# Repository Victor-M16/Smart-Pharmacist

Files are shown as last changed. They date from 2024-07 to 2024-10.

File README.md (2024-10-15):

# Smart Pharmacist

This project repository holds architecture and website source code for the Smart Pharmacist final year engineering project being implemented at [Malawi University Of Business And Applied Sciences](https://www.mubas.ac.mw/) by Victor Mjimapemba, Khumbolawo Mussa and Grace Chiwaya.

The project consists of a hardware and software element. The hardware element is an electronics project that is a rudimentary prototype of a carousel vending machine meant to dispense prescription medication. Further documentation for these componenents can be found in the `firmware` and `concepts` folders.

The software component is a built from the ground up hospital management system meant to work in tandem with the prototype. The main system is a django project named `smartpharmacist`

## Use Case Workflow
1. The patient completes a consultation with the doctor, who enters the prescription details into the web system, such as the patient's name, sickness and prescribed medication and instructions to take the medications.
2. The system automatically generates a unique 4-digit "prescription.code" which it assigns to the prescription the doctor just submitted.
3. The system sends an SMS message to the patient, containing the prescription.code, the names of the prescribed medications and the associated instructions. If the patient has no phone or their phone is off, the code is also displayed on the doctor's screen so the patient can copy it down on a paper or their physical health passport. 
4. The patient goes to the vennding machine prototype,which has already been boooted, has authenticated itself with the backend server using `jwt` and gone into `ready-state`. The patient then inputs the received "prescription.code" on the numeric keypad, using visual feedback from the 16x2 LCD module.
5. The machine goes into `code-validation-state` where it sends the received code to the backend server for processing as a POST request for security.
6. The backend server checks the code against its prescriptions database and if the code exists and corresponds to a prescription that has not been dispensed yet, then it queries the database for the medications assigned to this prescription and the vending slots where these pre-packaged medications were stored. The server responds to to the vending machine after this processing with either an error message if the code was invalid or a list of vending slots in optimised order for the vending machine to rotate to if the code was valid.
7. If the vending machine received a list of vending slots, then it goes into `dispensing-state` where it rotates in order of the received slots, allowing the patient to collect all their assigned medications.
8. The vending machine updates the prescription in the database so that itself and other vending machines know that that prescription code is no longer valid and has been dispensed.
9. The vending machine goes back into `ready-state` to be ready to service the next patient and code.

## Technologies 

1. [Django](https://docs.djangoproject.com/en/5.1/)
2. [Django-Rest-FrameWork](https://www.django-rest-framework.org/)
3. [HTML/CSS](https://developer.mozilla.org/en-US/docs/Learn/HTML/Introduction_to_HTML/Getting_started)
4. [Tailwind CSS](https://tailwindcss.com/)
5. [ArduinoIDE](https://www.arduino.cc/en/Guide)
6. [Twilio](https://www.twilio.com/en-us)
7. [Postgres](https://www.postgresql.org/)

## Hardware 

1. 16x2 LCD module. Ours uses (0x27) addressing. You need to check this.
2. ESP32
3. Arduino Uno
4. 4X4 Matrix Keypad
5. NEMA 17 Motors (17HS4023)
6. L298N Motor Drivers
7. Buzzer
8. Switch

## Setting Up The Project

1. Fork and clone this repository

2. Setup your Django development environment. More instructions [here](https://www.djangoproject.com/start/)

3. Make sure to also have node.js installed. Instructions [here](https://nodejs.org/)

4. Create a python virtual environment in the `smartpharmacist` directory

5. Install Django dependencies for the project using the `requirements.txt`

```shell
pip install requirements.txt
```
6. Install django-tailwind dependencies by navigating to `theme\static_src\` in your terminal and typing 

```shell
npm install
```
7. Create a `local_settings.py` file in the `smartpharmacist` directory and include the following Python code

```python
from .base_settings import *
```
Here you can specify any extra configuration specification to your environment, such as database connection.

8. Start the Tailwind Development server by running the following command in your terminal

```shell
python manage.py tailwind start
```

9. Start the Django development server by running the following command in your terminal:

```shell
python manage.py runserver
```

## Contributing To The Project

Feel free to contact the developers with any contributions you would like to make

- [Victor Mjimapemba](https://github.com/Victor-M16/)

- [Khumbolawo Mussa](https://github.com/Khumbolawo/)

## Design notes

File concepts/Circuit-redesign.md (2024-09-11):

Here’s a breakdown of the wiring and code examples for controlling a **stepper motor**, **16x2 LCD via I2C**, and a **4x4 keypad** with the ESP32.

### Wiring Diagrams:

#### 1. **Stepper Motor with L298N Motor Driver**:
- **IN1 (L298N)** → **GPIO 14 (ESP32)**
- **IN2 (L298N)** → **GPIO 27 (ESP32)**
- **IN3 (L298N)** → **GPIO 26 (ESP32)**
- **IN4 (L298N)** → **GPIO 25 (ESP32)**
- **GND (L298N)** → **GND (ESP32)**
- **12V power supply** for the motor should be connected to the L298N’s **power input**.

#### 2. **16x2 LCD with I2C Module**:
- **SDA (LCD)** → **GPIO 21 (ESP32)**
- **SCL (LCD)** → **GPIO 22 (ESP32)**
- **VCC** → **3.3V or 5V (ESP32)** (depending on your LCD module voltage requirements)
- **GND (LCD)** → **GND (ESP32)**

#### 3. **4x4 Keypad**:
- **Row 1 (Keypad)** → **GPIO 33 (ESP32)**
- **Row 2 (Keypad)** → **GPIO 32 (ESP32)**
- **Row 3 (Keypad)** → **GPIO 18 (ESP32)**
- **Row 4 (Keypad)** → **GPIO 19 (ESP32)**
- **Column 1 (Keypad)** → **GPIO 4 (ESP32)**
- **Column 2 (Keypad)** → **GPIO 5 (ESP32)**
- **Column 3 (Keypad)** → **GPIO 16 (ESP32)**
- **Column 4 (Keypad)** → **GPIO 17 (ESP32)**

---

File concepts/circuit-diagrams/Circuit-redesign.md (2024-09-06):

Here’s a breakdown of the wiring and code examples for controlling a **stepper motor**, **16x2 LCD via I2C**, and a **4x4 keypad** with the ESP32.

### Wiring Diagrams:

#### 1. **Stepper Motor with L298N Motor Driver**:
- **IN1 (L298N)** → **GPIO 13 (ESP32)**
- **IN2 (L298N)** → **GPIO 12 (ESP32)**
- **IN3 (L298N)** → **GPIO 14 (ESP32)**
- **IN4 (L298N)** → **GPIO 27 (ESP32)**
- **GND (L298N)** → **GND (ESP32)**
- **12V power supply** for the motor should be connected to the L298N’s **power input**.

#### 2. **16x2 LCD with I2C Module**:
- **SDA (LCD)** → **GPIO 21 (ESP32)**
- **SCL (LCD)** → **GPIO 22 (ESP32)**
- **VCC** → **3.3V or 5V (ESP32)** (depending on your LCD module voltage requirements)
- **GND (LCD)** → **GND (ESP32)**

#### 3. **4x4 Keypad**:
- **Row 1 (Keypad)** → **GPIO 32 (ESP32)**
- **Row 2 (Keypad)** → **GPIO 33 (ESP32)**
- **Row 3 (Keypad)** → **GPIO 25 (ESP32)**
- **Row 4 (Keypad)** → **GPIO 26 (ESP32)**
- **Column 1 (Keypad)** → **GPIO 34 (ESP32)**
- **Column 2 (Keypad)** → **GPIO 35 (ESP32)**
- **Column 3 (Keypad)** → **GPIO 36 (ESP32)**
- **Column 4 (Keypad)** → **GPIO 39 (ESP32)**

---

### Code Examples:

#### 1. **Stepper Motor Control** (via L298N):
Here’s a basic code for controlling the stepper motor using the L298N motor driver with the ESP32.

```python
import RPi.GPIO as GPIO
import time

# Pin Definitions for L298N
IN1 = 13
IN2 = 12
IN3 = 14
IN4 = 27

# Setup
GPIO.setmode(GPIO.BCM)
GPIO.setup(IN1, GPIO.OUT)
GPIO.setup(IN2, GPIO.OUT)
GPIO.setup(IN3, GPIO.OUT)
GPIO.setup(IN4, GPIO.OUT)

# Step sequence for the motor
step_sequence = [
    [GPIO.HIGH, GPIO.LOW, GPIO.HIGH, GPIO.LOW],
    [GPIO.LOW, GPIO.HIGH, GPIO.HIGH, GPIO.LOW],
    [GPIO.LOW, GPIO.HIGH, GPIO.LOW, GPIO.HIGH],
    [GPIO.HIGH, GPIO.LOW, GPIO.LOW, GPIO.HIGH]
]

def step_motor(delay, steps):
    for i in range(steps):
        for step in step_sequence:
            GPIO.output(IN1, step[0])
            GPIO.output(IN2, step[1])
            GPIO.output(IN3, step[2])
            GPIO.output(IN4, step[3])
            time.sleep(delay)

try:
    # Example: Run motor for 200 steps
    step_motor(0.01, 200)
except KeyboardInterrupt:
    pass
finally:
    GPIO.cleanup()
```

#### 2. **I2C LCD Control** (Using `LiquidCrystal_I2C` library):
You'll need the `LiquidCrystal_I2C` library to control the LCD. Install the library first:

```bash
pip install RPLCD
```

Code to display a message on the LCD:

```python
from RPLCD.i2c import CharLCD

# Initialize LCD (I2C address might differ)
lcd = CharLCD('PCF8574', 0x27)

# Clear display and show "Ready"
lcd.clear()
lcd.write_string('Ready')

# Move cursor and write on second row
lcd.cursor_pos = (1, 0)
lcd.write_string('Enter Code')
```

#### 3. **4x4 Keypad Input**:
You'll need the **Keypad library**. Install the `micropython-keypad` package.

```bash
pip install micropython-keypad
```

Here’s how to read input from the 4x4 keypad:

```python
from machine import Pin
from keypad import Keypad

# Define Keypad row and column pins
rows = [Pin(32, Pin.IN), Pin(33, Pin.IN), Pin(25, Pin.IN), Pin(26, Pin.IN)]
cols = [Pin(34, Pin.IN), Pin(35, Pin.IN), Pin(36, Pin.IN), Pin(39, Pin.IN)]

# Keypad matrix (4x4)
keys = [
    ['1', '2', '3', 'A'],
    ['4', '5', '6', 'B'],
    ['7', '8', '9', 'C'],
    ['*', '0', '#', 'D']
]

keypad = Keypad(keys, rows, cols)

def get_key():
    key = keypad.getKey()
    if key:
        print(f"Key pressed: {key}")
        return key

# Loop to capture keypad input
while True:
    key = get_key()
    if key:
        lcd.clear()
        lcd.write_string(f"Key Pressed: {key}")
```

### Integration:
- Once you have each of the components working individually, you can combine them into a single program where:
  - The **keypad** allows the user to input a code.
  - The **LCD** displays the input or other messages.
  - The **motor** runs based on keypad input or another trigger.

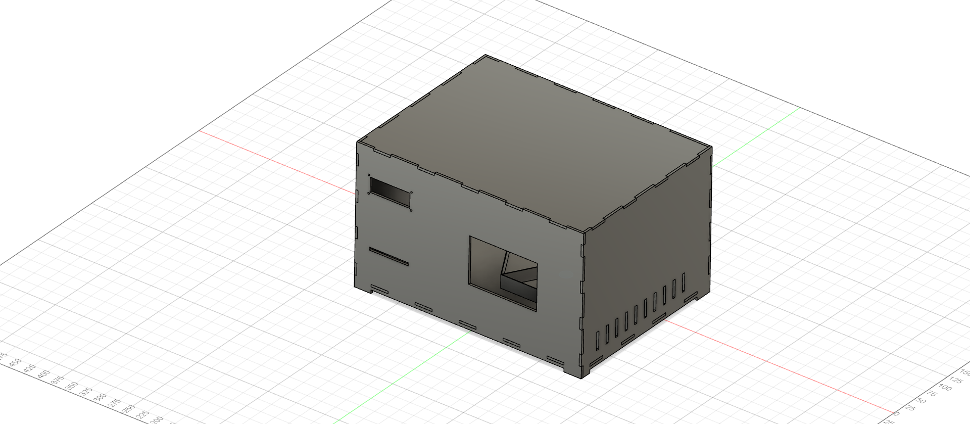
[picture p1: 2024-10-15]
concepts/3d-designs/SmartPharmacist.png

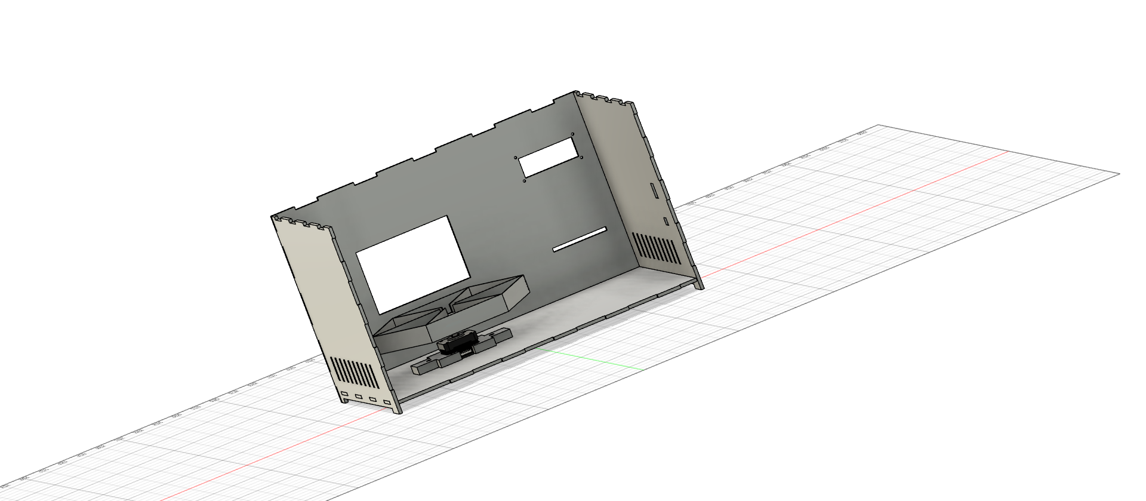
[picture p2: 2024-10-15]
concepts/3d-designs/Open.png

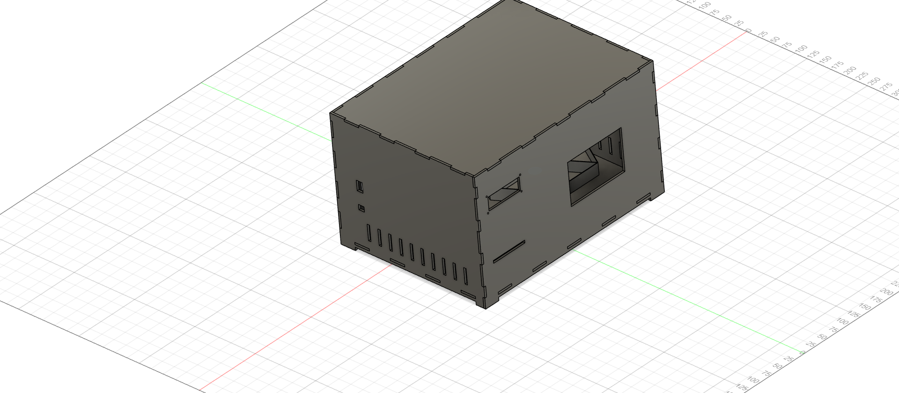
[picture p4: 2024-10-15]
concepts/3d-designs/Smart pharm.png

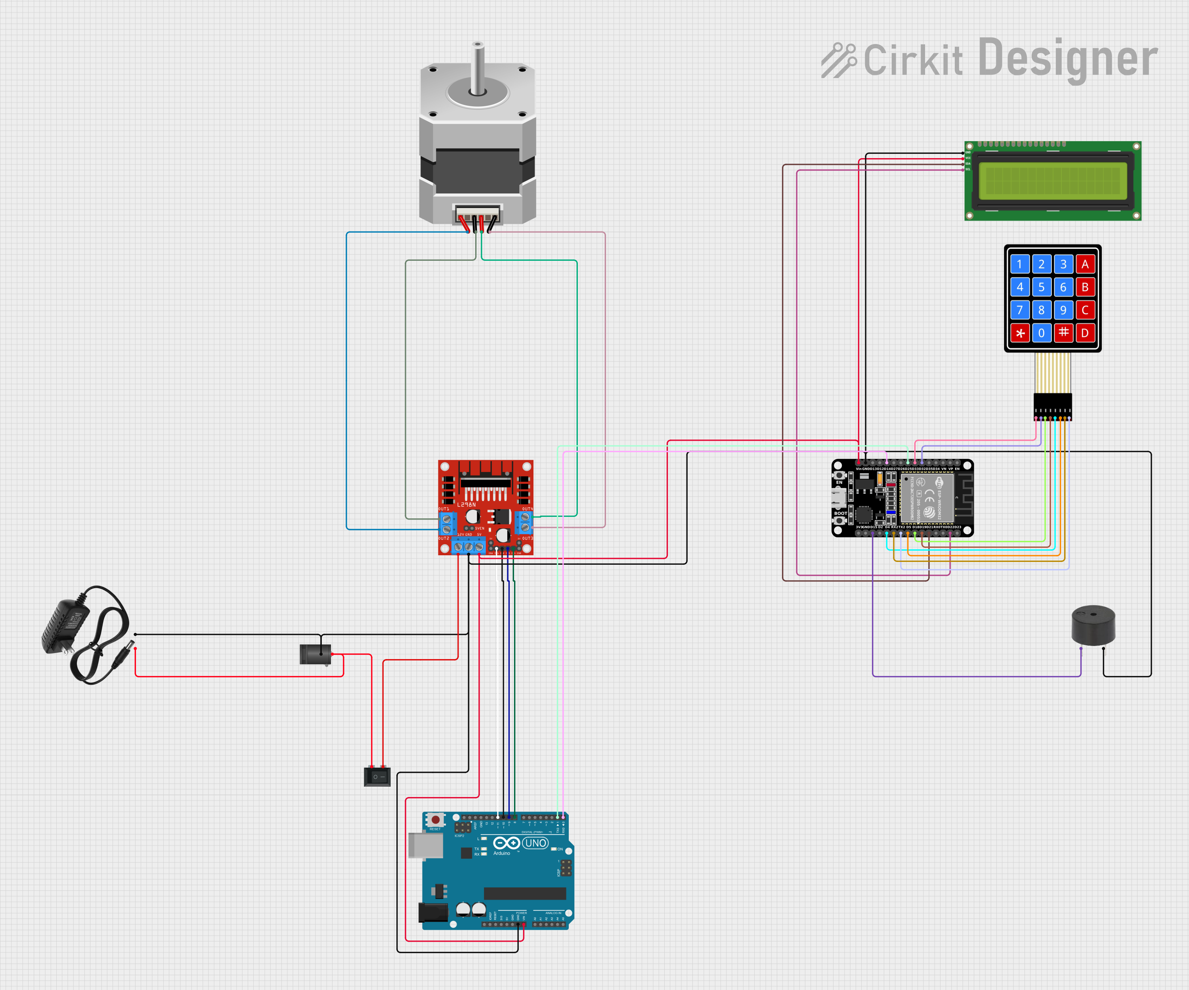
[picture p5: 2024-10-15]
concepts/circuit-diagrams/circuit_image.png

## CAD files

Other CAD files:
concepts/3d-designs/Casing v2.f3z

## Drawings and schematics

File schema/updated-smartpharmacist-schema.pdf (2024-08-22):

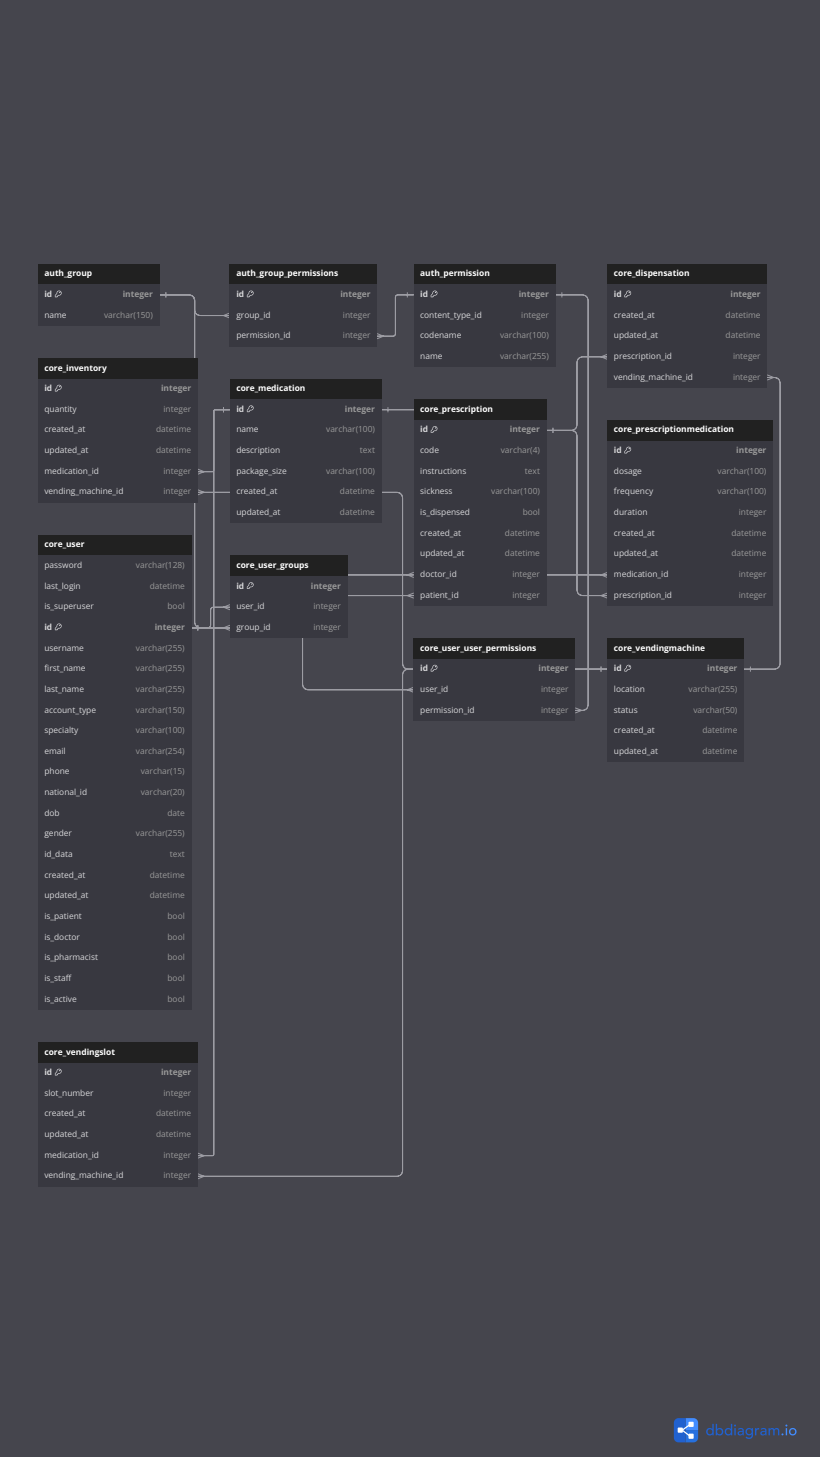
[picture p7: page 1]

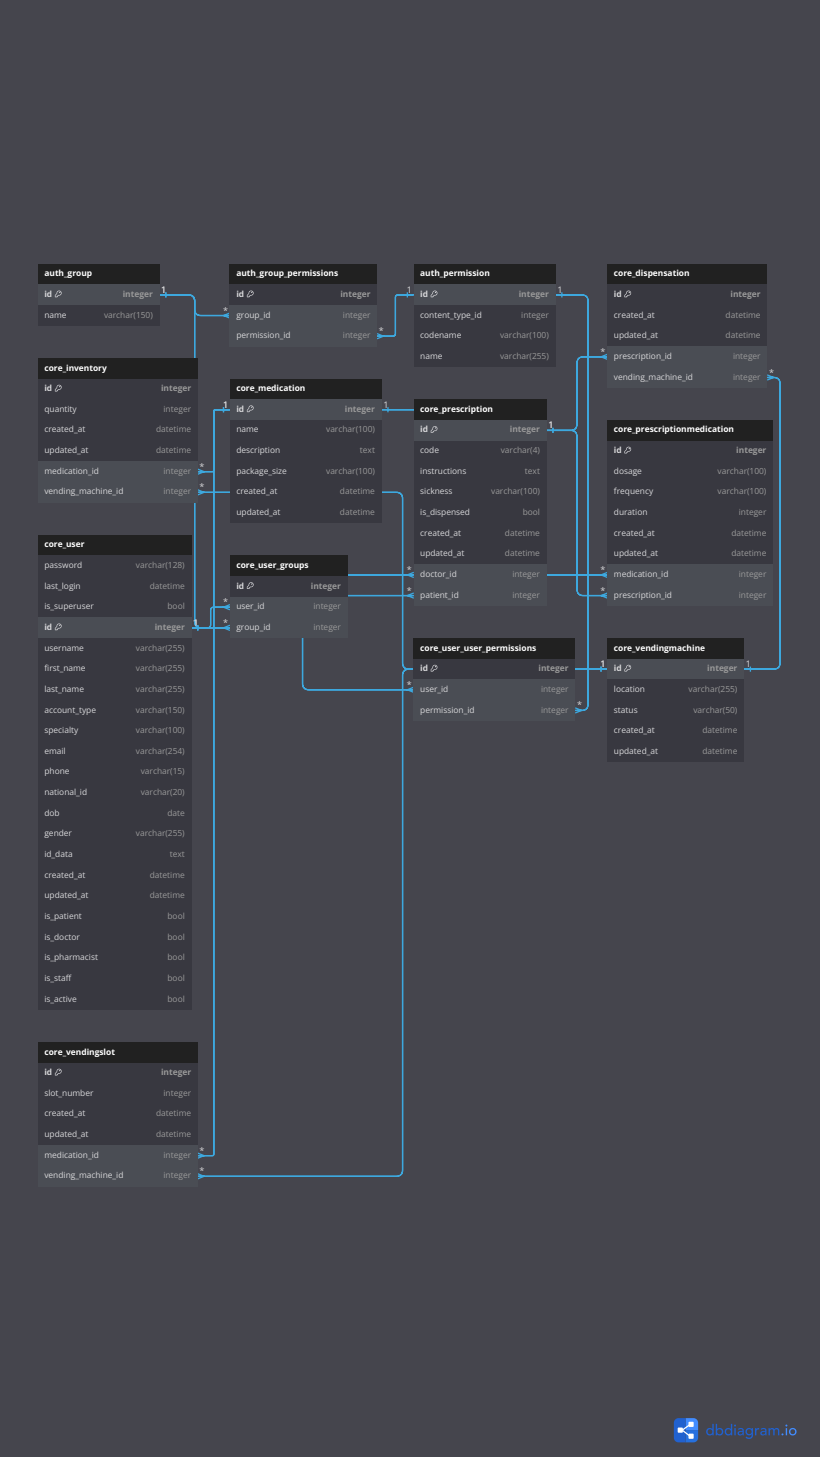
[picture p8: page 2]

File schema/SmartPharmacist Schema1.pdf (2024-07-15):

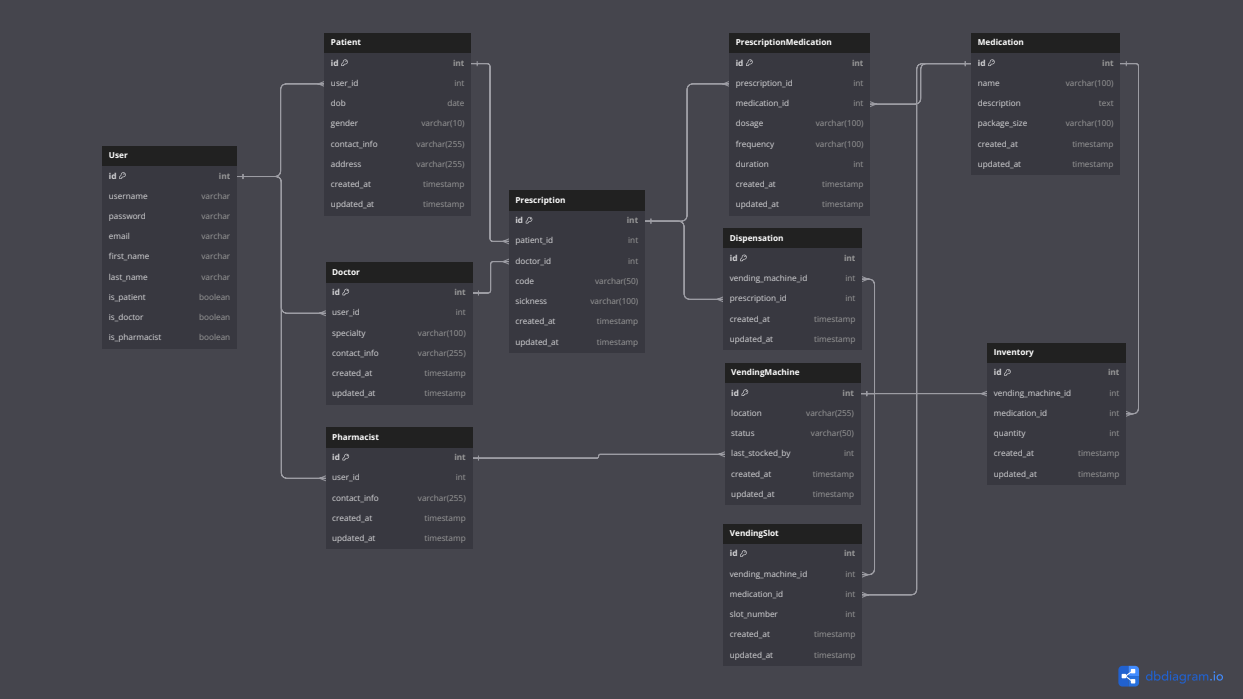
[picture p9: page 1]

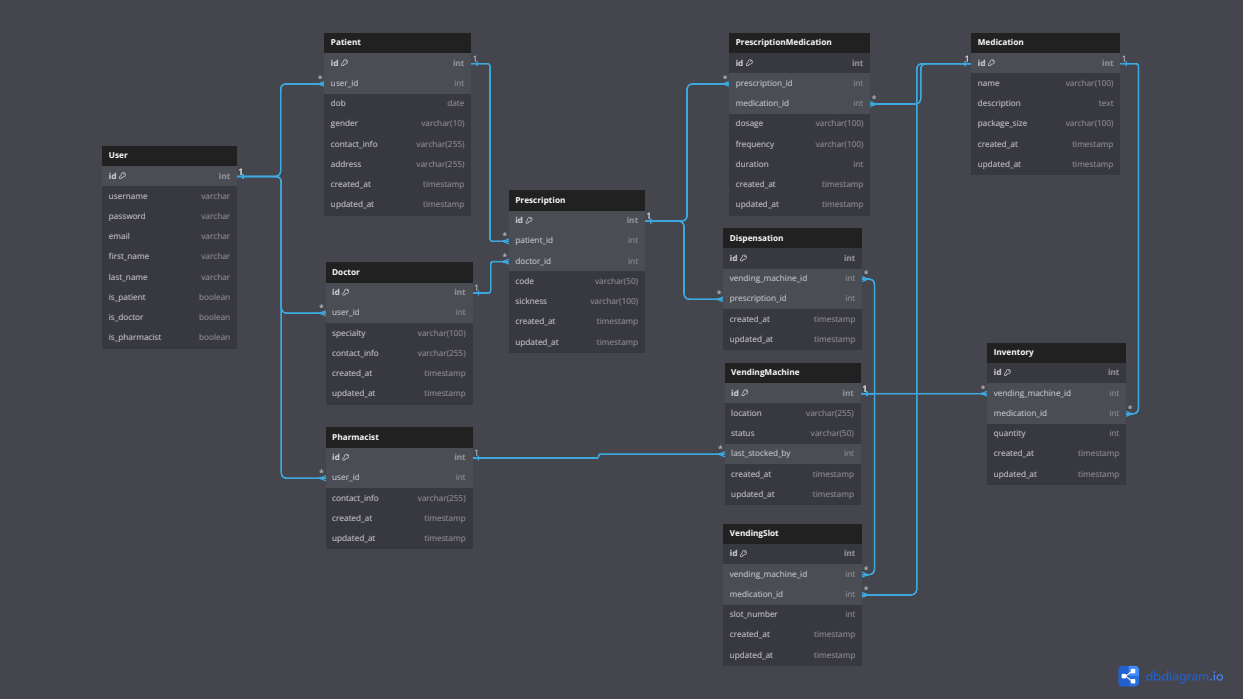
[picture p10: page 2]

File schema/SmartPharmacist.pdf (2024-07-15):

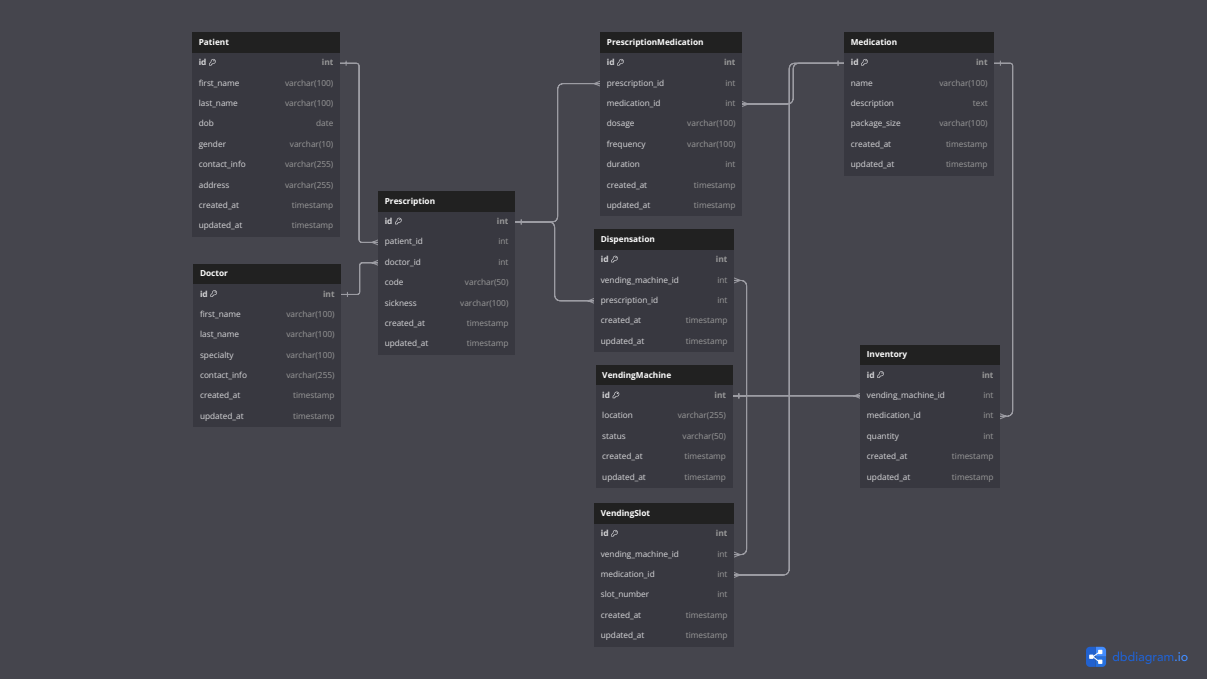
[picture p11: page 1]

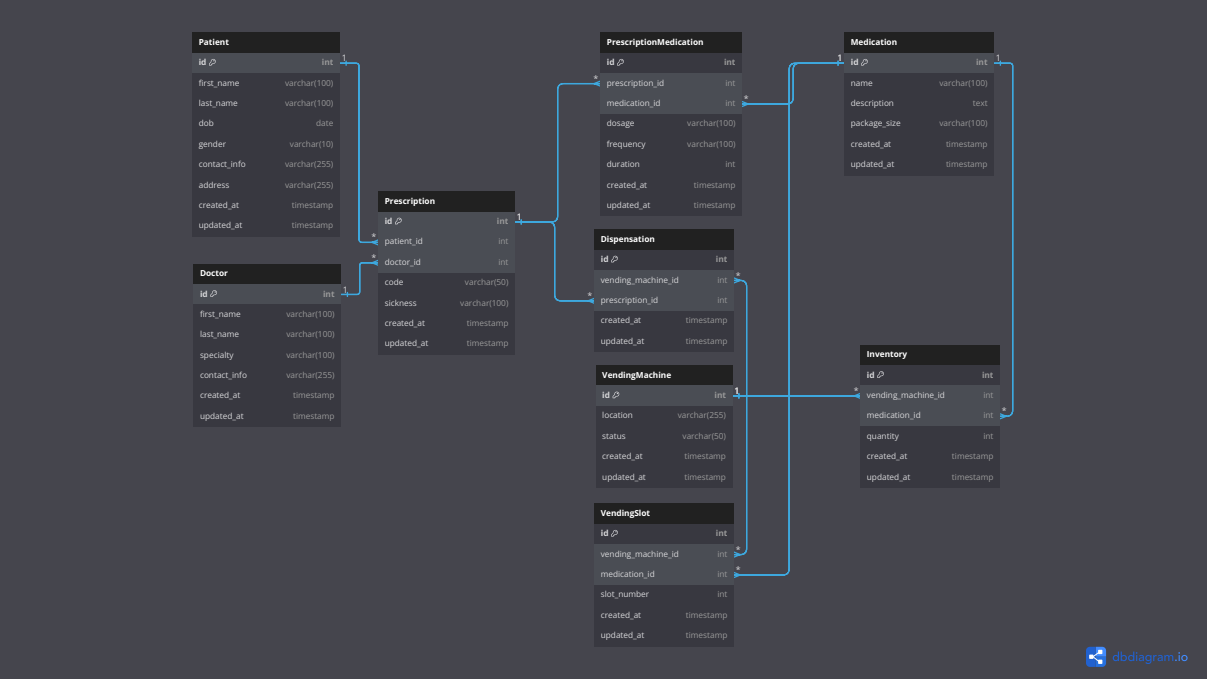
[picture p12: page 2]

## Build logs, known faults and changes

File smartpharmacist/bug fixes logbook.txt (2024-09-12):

The favicon was causing an internal server error that was difficult to debug when DEBUG = False, which was causing the error. 
`collectstatic` command was unable to find the favicon because it was located in the wrong directory while all the other images were in an app level static directory which was configured in the production_settings.py as '/static/'

this logging setup allowed quick debugging, might be useful in the future:

LOGGING = {
    'version': 1,
    'disable_existing_loggers': False,
    'handlers': {
        'file': {
            'level': 'ERROR',
            'class': 'logging.FileHandler',
            'filename': os.path.join(BASE_DIR, 'django_error.log'),
        },
    },
    'loggers': {
        'django': {
            'handlers': ['file'],
            'level': 'ERROR',
            'propagate': True,
        },
    },
}

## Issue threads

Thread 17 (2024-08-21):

Account created message is showing red instead of green, seems like a styling issue

Victor-M16, 2024-08-21:

Khumbolawo, 2024-08-22:
This code is meant for bootstrap classes. Since we are currently using Tailwind, we will have to find another way to dynamically apply styles based on the mesage tags

Khumbolawo, 2024-08-23:
Fixed with latest merge

Closed 2024-08-23.

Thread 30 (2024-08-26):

Forms need relevant logic attached to them using new api approach

Khumbolawo, 2024-08-26:
Not sure I fully understand how to do it yet but I'll try. You can takeover the issue if you'd rather do it/there's a way you'd rather do it

- [x] 1. New medication form (pharmacist view)
- [x] 2. New patient form (this one seems tricky? Since it needs the user model which has a bunch of stuff in it
- [x] 3. Rendering medications on pharmacist view as an inventory table or something
- [x] 4. Rendering prescriptions specific to the doctor view that created them

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
Victor-M16, 2024-08-26:
Not sure I fully understand how to do it yet but I'll try. You can takeover the issue if you'd rather do it/there's a way you'd rather do it

1. New medication form (pharmacist view): You can do this one
2. New patient form (this one seems tricky? Since it needs the user model which has a bunch of stuff in it: I will do this one
3. Rendering medications on pharmacist view as an inventory table or something: GET request to "api/medications"
4. Rendering prescriptions specific to the doctor view that created them: GET request to "api/prescriptions" but the viewset's `queryset` value should be filtered according to `request.user.id` or similar

Khumbolawo, 2024-08-26:
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
Stuck here. Dont know if the issue is in the APIs or my form code. LLMs don't seem to know either, been trying for 3 hours now.

The javascript im using for the post request is below

``` javascript
<script>
  document
    .getElementById("medication-form")
    .addEventListener("submit", function (event) {
      event.preventDefault();
      const formData = new FormData(document.getElementById("medication-form"));

      // Move the fetch call inside the function
      fetch("/api/medications/", {
        method: "POST",
        headers: {
          "Content-Type": "application/json",
          "X-CSRFToken": "{{ csrf_token }}",
        },
        body: JSON.stringify({
          name: formData.get("medication"),
          description: formData.get("description"),
        }),
      })
        .then((response) => response.json())
        .then((data) => {
          console.log("medication created:", data);
        })
        .catch((error) => {
          console.error("Error creating medication:", error);
        });
    });
</script>

```

Data seems like its being parsed correctly into json:
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

I double checked that the fields match with the model.

Khumbolawo, 2024-08-26:
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

Thinking these might be useful. Permission issues?

Khumbolawo, 2024-08-27:
1. New medication form done

Victor fixed the issue. Some leftover code in the medication viewsets from an earlier experiment was preventing the form from posting to the API successfully

Khumbolawo, 2024-08-27:
3. Rendering medications on pharmacist view, done.

Table design has changed a little bit. Looks more modern methinks. Will update the table styles on the other pages too

Closed 2024-09-04.

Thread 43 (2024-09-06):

Landing page required.

Victor-M16, 2024-09-06:
- [x] 1. Need the root url to not be the login screen but rather a landing page that describes the system. It will have a picture of the prototype, and us when completed.
- [x] 2. feel free to get some inspiration from various websites.
- [x] 3. Need some assets. The MUBAS logo and QECH logo should appear on the landing page.
- [x] 4. Create our own or use the MUBAS logo as the favicon. If created, it must also show up on the landing page together with the other two logos.
- [x] 5. The login screen on mobile view has no heading maybe its just my phone, but it seems to be unique to that page

Khumbolawo, 2024-09-10:
Done

Closed 2024-09-10.

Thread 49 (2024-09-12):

The tables seem a bit fluky. I don't know if its the ajax request to the API but they aren't working as expected, the bottom one (prescription medication table ) is consistent while the top one is not) need to look into this

Victor-M16, 2024-09-12:
The tables seem a bit fluky. I don't know if its the ajax request to the API but they aren't working as expected, the bottom one (prescription medication table ) is consistent while the top one is not) need to look into this

_Originally posted by @Victor-M16 in https://github.com/Victor-M16/Smart-Pharmacist/issues/41#issuecomment-2345019307_

Khumbolawo, 2024-09-12:
Problem was some of the api routes not being correct since we changed the overall routing for the rest of the site when the landing page came in. Fixed it

Closed 2024-09-12.

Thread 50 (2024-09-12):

Laser cut the casing with custom

Victor-M16, 2024-09-12:
The panels for the casing will be ready by tomorrow, will upload them inside the `concepts` folder

GraceChiwaya, 2024-09-12:
Alright noted

Victor-M16, 2024-10-03:
Cut the panels and assembled today. fits perfectly

Closed 2024-10-03.

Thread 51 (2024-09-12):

Laser cut the carousel with Custom

Victor-M16, 2024-09-12:
The carousel components will be ready in a few hours, need to test the stepper motor with load. We also need to find some threaded screws that fit on our stepper motor inorder to brace it from vibrating. Have an exciting design in mind actually. Should also explore more heat sinking possibilities to be on the safe side. After the 'landing page added' deployment we won't touch the website code again until the mechanical aspect of the prototype is done.

Here @GraceChiwaya will be crucial as she has been pushing that aspect of the project

Victor-M16, 2024-10-03:
This only partly worked. Strongly recommend 3d printing it instead

Closed 2024-10-03.

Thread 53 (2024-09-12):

Implement Pharmacist restock vending machine functionality

Victor-M16, 2024-09-12:
Basically a form that will allow the pharmacist to record the

- inventory
- medication
- vending machine
- vending slot

That they have just added.

The minute they press submit the system will update its records and guide patients to the correct vending machines accordingly.

The API approach we have been using should be used to keep the frontend and backend decoupled

Khumbolawo, 2024-09-12:
Forms created. They just need to actually do stuff now. Over to you 😢

Victor-M16, 2024-09-12:
Will get to it

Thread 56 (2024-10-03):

Edit landing page, replace sqlite with postgres on technology used

Victor-M16, 2024-10-03:

Closed 2024-10-03.

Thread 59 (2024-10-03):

Populate the database with medications

Victor-M16, 2024-10-03:
Select 6 of the most commonly prescribed medications at QECH and assign them to the slots

Khumbolawo, 2024-10-04:
Adding the following from doctor Chisomo's recommendation

Painkillers
1. paracetamol
2. ibuprofen

Antibiotics
1. Amoxicillin
2. Cotrimoxazole (bactrim)
3. Erythromycin

Anti-hypertensives
1. Hydrochlorothiazide
2. Furosemide
3. Spinorolactone

Doctor Chisomo is finding me some market versions of some of these as of right now

Khumbolawo, 2024-10-04:
Added them on vending slots. Closing this issue

Closed 2024-10-04.

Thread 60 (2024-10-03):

Implement Buzzer logic, LED logic and server-based current_slot initialisation in the firmware

Victor-M16, 2024-10-03:
-There are plans to add a buzzer and LED strip to the machine to make the carousel more visible when the machine is closed.

- [ ] Implement the logic in the software

- [ ] The machine is a stateful machine in that its most recent slot is relevant to its future actions. Implement logic to store the current slot of the machine on the server after it finishes a dispensation
(we can assume it finishes a dispensation)

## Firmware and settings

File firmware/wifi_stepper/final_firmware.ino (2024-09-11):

#include <Stepper.h>
#include <Keypad.h>
#include <Wire.h>
#include <LiquidCrystal_I2C.h>
#include <WiFi.h>
#include <HTTPClient.h>
#include <WiFiClientSecure.h>
#include <ArduinoJson.h>

// for the stepper motor
const int steps_per_rev = 200;  // Set to 200 for NEMA 17
#define IN1 14
#define IN2 27
#define IN3 26
#define IN4 25

// for the keypad
#define ROWS  4
#define COLS  4

// Configuration
//replace with wifi credentials
const char* ssid = "";
const char* password = "";
const char* tokenUrl = "https://smart-pharmacist-production.up.railway.app/api/token/";
const char* esp32Url = "https://smart-pharmacist-production.up.railway.app/api/esp32/";

const uint8_t vendingMachineId = 1;

// SSL Root Certificate for HTTPS (replace with your server’s certificate)
const char* root_ca = R"literal(
-----BEGIN CERTIFICATE-----
...
-----END CERTIFICATE-----
)literal";

// configure the keypad
char keyMap[ROWS][COLS] = {
  {'1','2','3', 'A'},
  {'4','5','6', 'B'},
  {'7','8','9', 'C'},
  {'*','0','#', 'D'}
};

uint8_t rowPins[ROWS] = {33, 32, 18, 19};  // GPIO33, GPIO32, GPIO18, GPIO19
uint8_t colPins[COLS] = {4, 5, 16, 17};    // GPIO4, GPIO5, GPIO16, GPIO17
Keypad keypad = Keypad(makeKeymap(keyMap), rowPins, colPins, ROWS, COLS);

uint8_t LCD_CursorPosition = 6;  // Start after "Code: "
bool isReady = true;  // Flag to indicate if the system is in ready state
String jwtToken = "";
String inputCode = "";

// configure the display
LiquidCrystal_I2C lcd(0x27, 16, 2);  // set the LCD address to 0x27 for a 16 chars and 2 line display

// configure the motor
Stepper motor(steps_per_rev, IN1, IN2, IN3, IN4);

// Global variable to keep track of the motor's current slot
uint8_t currentSlot = 1;  // Assuming the motor starts at slot 1 (or a known home position)


void setup() {
  Serial.begin(115200);

  // initialize the motor speed
  motor.setSpeed(60);

  // initialize the LCD
  lcd.init();
  lcd.backlight();
  lcd.setCursor(0, 0);
  lcd.print("Connecting WiFi...");

  // connect to WiFi
  WiFi.begin(ssid, password);
  while (WiFi.status() != WL_CONNECTED) {
    delay(500);
    Serial.print(".");
  }

  Serial.println("\nConnected to WiFi");
  lcd.clear();
  lcd.setCursor(0, 0);
  lcd.print("WiFi Connected");

  // Authenticate and get JWT token
  if (authenticate()) {
    lcd.clear();
    lcd.setCursor(0, 0);
    lcd.print("Authenticated");
    delay(3000);
    lcd.clear();
    lcd.setCursor(0, 0);
    lcd.print("Code: ");
  } else {
    lcd.clear();
    lcd.setCursor(0, 0);
    lcd.print("Auth Failed");
  }

  displayReadyMessage();  // Display the scrolling ready message
}

void loop() {
  if (isReady) {
    displayReadyMessage();
  }

  char key = keypad.getKey();

  if (key) {
    if (isReady) {
      lcd.clear();
      isReady = false;  // Stop displaying the ready message once input starts
      lcd.setCursor(0, 0);
      lcd.print("Code: ");
      lcd.setCursor(0, 1);
      lcd.print("Kuyambanso: C");
    }

    if (key == 'C') {
      resetToReadyState();
    } else {
      Serial.print(key);

      lcd.setCursor(LCD_CursorPosition++, 0);
      lcd.print(key);
      inputCode += key;  // Append the key to the input code

      if (inputCode.length() == 4) {
        processCode(inputCode);
        resetToReadyState();
      }
    }
  }
}

// API functions
bool authenticate() {
  WiFiClientSecure client;
  client.setCACert(root_ca);  // Attach the SSL certificate

  HTTPClient http;
  http.begin(client, tokenUrl);  // Use HTTPS with secure client

  String postData = "{\"username\":\"****\",\"password\":\"***\"}";
  http.addHeader("Content-Type", "application/json");
  int httpResponseCode = http.POST(postData);

  if (httpResponseCode > 0) {
    String response = http.getString();
    DynamicJsonDocument doc(1024);
    deserializeJson(doc, response);
    jwtToken = doc["access"].as<String>();  // Extract the JWT token
    Serial.println("Authenticated. JWT Token: " + jwtToken);
    http.end();
    return true;
  } else {
    Serial.print("Error on sending POST: ");
    Serial.println(httpResponseCode);
    http.end();
    return false;
  }
}

std::vector<int> fetchVendingSlots() {
  WiFiClientSecure client;
  client.setCACert(root_ca);  // Attach the SSL certificate

  HTTPClient http;
  http.begin(client, esp32Url);  // Use HTTPS with secure client

  http.addHeader("Content-Type", "application/json");
  http.addHeader("Authorization", "Bearer " + jwtToken);

  String postData = "{\"code\":\"" + inputCode + "\", \"current_slot\": " + String(currentSlot) + ", \"vending_machine_id\": " + String(vendingMachineId) + "}";
  int httpResponseCode = http.POST(postData);

  std::vector<int> vendingSlots;

  if (httpResponseCode > 0) {
    String response = http.getString();
    Serial.println("Response: " + response);

    // Parse the JSON response
    DynamicJsonDocument doc(1024);
    deserializeJson(doc, response);

    // Check if "vending_slots" is present
    if (doc.containsKey("vending_slots")) {
      JsonArray slots = doc["vending_slots"].as<JsonArray>();
      
      // Iterate through the array and populate the list
      for (int i = 0; i < slots.size(); i++) {
        vendingSlots.push_back(slots[i].as<int>());
      }
    } else {
      Serial.println("Error: 'vending_slots' not found in the response");
    }

  } else {
    lcd.clear();
    lcd.setCursor(0, 0);
    lcd.print("Error: No Resp");
    Serial.println("Error: No response from server");
  }

  http.end();
  return vendingSlots;
}

void createDispensation(std::vector<int> vendingSlots) {
  // Rotate motor based on each vending slot received
  if (!vendingSlots.empty()) {
    for (int slot : vendingSlots) {
      rotateMotorToSlot(slot);  // Rotate to the correct slot
      delay(1000);  // Simulate delay for dispensing medication
    }
  } else {
    lcd.clear();
    lcd.setCursor(0, 0);
    lcd.print("No Slots Found");
  }
}

void rotateMotorToSlot(int slot) {
  int steps_per_slot = steps_per_rev / 6;  // Assuming 6 slots for the motor rotation
  int targetSlot = slot; 

  // Calculate the difference in steps based on the current position
  int slotDifference = targetSlot - currentSlot;  // Difference between target and current slot
  int steps_to_move = steps_per_slot * slotDifference;  // Steps needed to move to the target slot

  // Rotate the motor by the calculated number of steps
  motor.step(steps_to_move);  

  // Update the currentSlot to reflect the new position
  currentSlot = targetSlot;

  // Provide feedback on the LCD
  lcd.clear();
  lcd.setCursor(0, 0);
  lcd.print("Vending slot: ");
  lcd.setCursor(0, 1);
  lcd.print(slot);

  // Print the action to the serial monitor for logging
  Serial.println("Dispensing medication at slot: " + String(slot));
  delay(3000);
}

// Main logic
void processCode(String code) {
  Serial.println("\nProcessing Code: " + code);

  lcd.clear();
  lcd.setCursor(0, 0);
  lcd.print("Code yanu: " + code);

  lcd.setCursor(0, 1);
  lcd.print("Dikilani pangono");

  std::vector<int> vendingSlots = fetchVendingSlots(); 

  Serial.println("slots fetched successfully");

  createDispensation(vendingSlots);  // Call the function to dispense medication
  Serial.println("medication dispensed");

}

// LCD functions
void resetToReadyState() {
  inputCode = "";  // Clear the input code
  LCD_CursorPosition = 6;  // Reset position after "Code: "
  lcd.clear();
  isReady = true;
  displayReadyMessage();  // Display the ready message again
}

void displayReadyMessage() {
  scrollMessage("Ready. Lowetsani Vending Code ", 0);  // Scroll on the top row
}

void scrollMessage(String message, uint8_t row) {
  static unsigned long lastScrollTime = 0;
  static int scrollPos = 0;

  if (millis() - lastScrollTime >= 300) {  // Adjust the scroll speed here
    lastScrollTime = millis();
    lcd.setCursor(0, row);
    lcd.print(message.substring(scrollPos, scrollPos + 16));
    scrollPos++;
    if (scrollPos > message.length()) {
      scrollPos = 0;  // Reset scroll position to start again
    }
  }
}

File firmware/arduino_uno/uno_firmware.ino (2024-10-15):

#include <Arduino.h>
#include <Stepper.h>

// Number of steps per output rotation
const int steps_per_rev = 200; // Number of steps for a full revolution (depends on your stepper motor)
const int steps_per_slot = steps_per_rev / 6; // Steps per 60-degree rotation

// Create Instance of Stepper library
Stepper myStepper(steps_per_rev, 8, 9, 10, 11);

int currentSlot = 6;
void setup() {

    // Set the speed at 20 rpm:
    myStepper.setSpeed(20);
    // Initialize the serial port:
    Serial.begin(9600);

    if (Serial.available()) {
      String dataFromESP = Serial.readStringUntil('\n');
      Serial.println("Booting Data received from ESP32: " + dataFromESP); // Output received data

      currentSlot = parseSlot(dataFromESP); // Initialize the current slot from the server
    }
    Serial.println("Setup complete");
}

void loop() {
    // Check if data is available from ESP32
    if (Serial.available()) {
        String dataFromESP = Serial.readStringUntil('\n');
        Serial.println("Data received from ESP32: " + dataFromESP); // Output received data

        // Parse the received string into an integer
        int targetSlot = parseSlot(dataFromESP);
        
        // Rotate the motor to the specified slot
        rotateMotorToSlot(targetSlot);

        delay(2000); // Delay to allow collection 
    }
}

// Function to parse the received string into an integer
int parseSlot(const String& data) {
    // Convert the received string to an integer
    return data.toInt(); // Return parsed integer
}

// Function to rotate the motor to the target slot
void rotateMotorToSlot(int targetSlot) {
    // Ensure the targetSlot is valid (0 to 5 for 6 slots)
    if (targetSlot < 1 || targetSlot >= 7) {
        Serial.println("Invalid slot number. Must be between 1 and 6.");
        return;
    }

    if (targetSlot == currentSlot) {
        // If the target slot is the same as the current slot, no need to move
        Serial.println("Motor is already at the target slot.");
        return;
    }

    // Calculate the shortest direction to rotate
    int slotDifference = targetSlot - currentSlot;
    
    // If the difference is negative, the motor needs to rotate backward
    if (slotDifference < 0) {
        slotDifference += 6;  // Adjust for circular behavior (6 slots)
    }

    // Check if rotating forward or backward is shorter
    int stepsForward = slotDifference * steps_per_slot;
    int stepsBackward = (6 - slotDifference) * steps_per_slot;

    if (stepsForward <= stepsBackward) {
        // Rotate forward
        myStepper.step(stepsForward);
        Serial.println("Rotating forward by " + String(stepsForward) + " steps to slot " + String(targetSlot));
    } else {
        // Rotate backward
        myStepper.step(-stepsBackward);
        Serial.println("Rotating backward by " + String(stepsBackward) + " steps to slot " + String(targetSlot));
    }

    // Update the current slot
    currentSlot = targetSlot;

    // Send the current slot back to the ESP32
    Serial.println("Current slot: " + String(currentSlot));
    delay(1000); // Optional delay after sending the current slot
}

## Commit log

2024-07-06 feat: :sparkles: Add basic patient view
2024-07-15 -added pharmacist model for access to vending machines and restocking purposes -added List and Create API endpoints and some of their urls as well -began implementation of access control features for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
2024-07-17 refactor: :arrow_up: Add flowbite component library to project
2024-07-17 feat: :sparkles: Add patient creation form
2024-07-18 test: :bug: Attempt to fix flowbite installation issues
2024-07-31 pre-ESP32 config
2024-08-01 fix: :arrow_up: Fix flowbite js
2024-08-17 Revert "began refactoring codebase into CBVs from FBVs and organised imports using isort."
    [urls.py, views.py]
2024-08-17 fixed some routing issues and added messages to registration and login
    [urls.py, views.py]
2024-08-18 update styles for new patient page
2024-08-18 update patient views to new styles
2024-08-18 added logout view and created button to handle logout requests
2024-08-21 registration fixed with valdation messages
    [views.py]
2024-08-24 fix: :bug: reconfigured API permissions
    [custom_permissions.py, views.py]
2024-08-27 patient submission working
2024-08-27 changed user model to accommodate patient form submission
2024-08-27 feat: :bug: fix new prescription script not completing
    [views.py]
2024-08-27 feat: :heavy_plus_sign: twilio is now working, further testing is required to find out how to fix sms issues
    [views.py]
2024-08-29 filter prescriptions by doctor
2024-08-29 fixed filtering of prescriptionMedications
    [views.py]
2024-09-04 feat(Firmware): :lock: established secure communication between esp32 and backend server
    -using jwt to authenticate the esp32 -also got keypad and lcd working -offloaded code processing logic to the server to address potential memory issues in ESP32
    ESP32 loses access if the server restarts. Need a schedule for refreshing token
    [urls.py, views.py]
2024-09-04 fix(Design): :art: added a basic 3d concept of the vending machine
    [Casing v2.f3z]
2024-09-06 feat(Firmware): :tada: beginning full embedded system integration of electronics (without mechanical/structural parts)
    -motor tested and working, the L298N built in heat sink is doing its job but might need to refine the casing design with ventilation to prevent heating -have to rewire to accommodate the keypad, stepper motor, LCD and a switch button to turn the machine on. -changes to make to 3d render include -add ventilation slits -add entry point for power supply cabling -add holes for fastening the LCD -might need to do it without sliding doors for now
    the firmware needs to be restructured because the circuit wiring has changed
    [basicStepper.ino, serializers.py]
2024-09-08 feat: :sparkles: initial commit for landing page
2024-09-08 feat: :sparkles: add technologies section to landing page
2024-09-08 feat: :sparkles: add initial design for landing page
2024-09-08 initial landing page mobile layouts
2024-09-09 Update urls.py
    Fix home route to use a different path
    [urls.py]
2024-09-10 style: :lipstick: add static files to landing page
2024-09-11 added filtering of vending slots based on the machine that made the request
2024-09-11 feat(Firmware): :art: improved firmware files to keep order + uploaded near final version of firmware (excluding servo control)
    -firmware and electronics are pretty much sorted. Remaining part is the mechanical side. 3D models need to be finalised pronto
    uploading a new sqlite copy with updated passwords. dont think anything major will break but new passwords will be needed
2024-09-12 added landing page
2024-09-12 update lightmode styles on landing page
2024-09-12 add slot selection to restock form
2024-09-16 fixed table not showing issues
    [views.py]
2024-10-03 fixed prescriptions ordering and added current_slot attribute to track state of vending machine
    [views.py]
2024-10-15 docs: :memo: added new circuit diagrams, new firmware and updated landing page and README
